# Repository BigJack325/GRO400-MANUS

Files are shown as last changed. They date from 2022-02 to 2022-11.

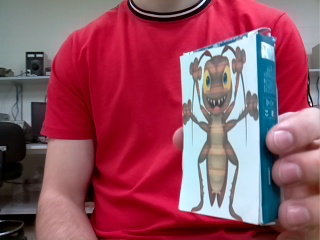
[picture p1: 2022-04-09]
Hexapod-master/Hexapod_Qt/Tensorflow/workspace/images/collectedimages/Angry/Angry.ae11384a-b84e-11ec-aec1-dca632b24006.jpg

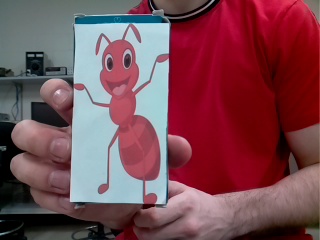
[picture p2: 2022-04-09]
Hexapod-master/Hexapod_Qt/Tensorflow/workspace/images/collectedimages/Happy/Happy.29205612-b84d-11ec-aec1-dca632b24006.jpg

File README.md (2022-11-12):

# GRO400-MANUS
4th Semester Upgraded Hexapod Project for Robotique Engineering Sherbrooke University

<div id="ManUS" align="center">
    <h1>ManUS</h1>
    <h3>Hexapod Robot : Upgraded Version | Promo66-UdeS-GRO</h3>
</div>
<div id="badges" align="center">
    


 

</div>

**This academic project is based on an older academic project from robotic engineering undergraduates at Université de Sherbrooke. "Manu" is an hexapod robot able to interact with his environments. Along with 6 legs comes a camera mounted on a 3D printed head, elevating Manu to a whole new level of robotic hexapod. It can walk, look around and chase targets all around him in a restrained area/arena.**

## Table of Contents
- [Setup](#Setup)
    - [Setup for Users](#SetupUsers)
- [Documentation](#Documentation)
    - [Servos Classification](#Servosclassification)
    - [Assembly Guide](#assemblyguide)
    - [Electrical Schematic](#electricalschematic)
    - [Electrical Diagram of the Shield](#electrical)
    - [Code Overview](#Codeexplication)
- [Robot Operation](#Operation)
    - [Robot Movement](#Movement)
    - [Robot Vision](#Vision)
    - [HMI And Robot Controls](#Controls)
- [External Resources](#Ressources)
    - [Battery, Power Source, and Charger](#Battery)
    - [Microcontroller Board](#Controller)
    - [On-Board Computer](#Computer)
    - [Servomotor for the legs](#Servo1)
    - [Servomotor for the mandibles](#Servo2)
    - [Current Sensor](#Current)
    - [DC/DC Converter](#DCDC)
    - [Fuse 10 Amp](#Fuse)

## Setup

#### Setup for Users

<b>Step 1.</b> Connect Raspberry Pi camera to the Raspberry Pi before booting it up;
<br/>
<b>Step 2.</b> Clone this repository: https://github.com/EDP325/GRO400-MANUS.git
<br/>
<b>Step 3.</b> Create a new virtual environment, install dependencies, and add virtual environment to the Python Kernel by running in terminal:
<pre>
cd ./Hexapod-Master/Hexapod_Qt
./install_venv_pi.sh
</pre> 
<b>Step 4.</b> Connect the hexapod's microcontroller (Arduino) to Raspberry Pi;
<br/>
<b>Step 5.</b> Open the file <b>main.cpp</b> in the <b>./Hexapod-Master/Hexapod_Arduino/src</b> folder, and build the code into the microcontroller with your favorite IDE with PlatformIO;
<br/>
<b>Step 6.</b> Upload the <b>main.cpp</b> in the Arduino;
<br/>
<b>Step 7.</b> Run the file <b>MANUS_QT</b> in the <b>./Hexapod-Master/Hexapod_Qt</b> folder;
<br/>
<b>Step 8.</b> Initialize the serial communication.

## Documentation
#### <a id = "Servosclassification">Classification of the robot servos:</a>

photo patte hexapod

#### <a id= "assemblyguide">Assembly Guide</a>
You need to 3D print the necessary parts that you can find in the *./CAD* folder.   
We have a complete assembly guide [here](https://github.com/EDP325/GRO400-MANUS/wiki):

#### <a id = "electricalschematic"> Electrical Schematic</a>
Schema fritzing
#### <a id= "electrical">Electrical Diagram of the Shield: </a>


#### <a id="Codeexplication">Code Overview</a>

The code is divided in two main sections. The first one is all about the robot's movment and is written in C++ and is run on the Arduino.  This code uses switch cases depending one the manuel/automatic mode and which movment to do.
The second section  includes the vision algorithm and the HMI.  It is written in Python and is run on the Raspberry Pi.  It is made to detect the chosen images and display  the HMI, a screen connected to the Pi.  We chose to use VNCviewer to connect to the Raspberry Pi through Wifi to have a remote connection to the hexapod.

## Robot Operation

#### Robot Movement
The robot can move forward, backward and sideways.  It can also rotate clockwise and counterclockwise.  The head can rotate and the mandibles can open cand close.  

#### Robot Vision
The robot has a vision algorithm that detects these two images: 

happyangry

#### HMI And Robot Controls
Our HMI shows:
- The current view of the cam with TensorFlow AI detection;
- The angles of all the servos;
- A map of the arena with the position of the hexapod;
- Informations for the camera and messages from the Arduino
- Information about battery voltage percentage
- A graphic that shows the the value of a variable over time
- A ComboBox to see every connected ports to initialize serial communication
- Buttons to move the robots



## External ressources

Under this section, you will find external links and descriptions of the project's external resources.

#### Battery

- Brand Name: Makita
- Model:
    - Battery: BL1041B
    - Power Source: PE00000028
    - Charger: DC10SB
- ASIN:
    - Battery: B017GQJDVM
    - Charger: B01FY4XCB0
- Information / Resources:
    - [Makita Battery Webpage](https://www.makitatools.com/products/details/BL1041B)
    - [Makita Power Source Webpage](https://www.makitatools.com/products/details/PE00000028)
    - [Makita Charger Webpage](https://www.makitatools.com/products/details/DC10SB)

#### Microcontroller board

- Brand Name: Arduino
- Model: Mega 2560 R3 (A000067)
- ASIN: B0046AMGW0
- Information / Resources: [Arduino Webpage](https://store.arduino.cc/mega-2560-r3)

#### Onboard computer

- Brand Name: Raspberry Pi
- Model: 3B
- ASIN: B01LPLPBS8
- Information / Resources: [Raspberry Pi Webpage](https://www.raspberrypi.org/products/raspberry-pi-3-model-b/)

#### Servomotor for the legs

- Brand Name : VIPMOON
- Model : MG996R
- Information / Resources : [Amazon Webpage](https://www.amazon.ca/-/fr/gp/product/B07VT5T9JC/ref=ewc_pr_img_1?smid=A2FI4MJY3VQVX5&psc=1)

#### Servomotor for the mandibles

- Model : MG90S
- Information / Resources : [Amazon Webpage](https://www.amazon.ca/servomoteur-h%C3%A9licopt%C3%A8re-m%C3%A9tallique-intelligent-commandes/dp/B08W26FNQD/)
#### Current sensor

- Brand Name : ROBOJAX
- Model : ACS712
- ASIN :B07YP4693C
- Information / Resources : [Amazon Webpage](https://www.amazon.ca/gp/product/B07YP4693C/ref=ppx_yo_dt_b_asin_title_o02_s00?ie=UTF8&psc=1)

#### DC/DC Converter

- Brand Name : Tyenaza
- Model : Tyenazad03xwg94zo
- ASIN :
- Information / Resources : [Amazon Webpage](https://www.amazon.ca/gp/product/B097QT54C7/ref=ppx_yo_dt_b_asin_title_o02_s00?ie=UTF8&amp&psc=1)

#### Pi Camera

- Brand Name : Keyestudio
- Model : 8541582798
- ASIN :
- Information / Resources : [Amazon Webpage](https://www.amazon.ca/gp/product/B073RCXGQS/ref=ppx_yo_dt_b_asin_title_o01_s00?ie=UTF8&psc=1)
    
fuse 10 AMP
#### <a id="Fuse">Fuse 10 AMP 250V</a>

- Brand Name : Littelfuse
- Model : Littelfuse 5x15MM. FAST ACTING 10A.250V.
- Information / Resources :You can buy fuse at any electronics store near your house.  We bought ours [here](https://electro5.com/fr/product/231621/littlefuse-5x15mm-fast-acting-10a250v/)

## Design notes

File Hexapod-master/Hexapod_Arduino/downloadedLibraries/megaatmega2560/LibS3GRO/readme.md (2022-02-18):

# Librairie pour Arduino et carte ArduinoX
voir le wiki pour plus d'informations

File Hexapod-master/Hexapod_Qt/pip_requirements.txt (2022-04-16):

opencv-python-headless
PyQtChart
wget
imutils
ipykernel
lxml

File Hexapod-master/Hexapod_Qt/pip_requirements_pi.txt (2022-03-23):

opencv-python-headless
PyQtChart
imutils
lxml
picamera

https://github.com/google-coral/pycoral/releases/download/v2.0.0/tflite_runtime-2.5.0.post1-cp39-cp39-linux_armv7l.whl

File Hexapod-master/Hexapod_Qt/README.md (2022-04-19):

## Installation on Raspberry-Pi:

<b>Step 1.</b> Activate Raspberry-Pi VNC and  legacy camera using <b>sudo raspy-config</b>  in the interface options selection
<br/>
<b>Step 2.</b> Install VSCode using
<pre>
sudo apt-get code
</pre>
<b>Step 3.</b> Execute the <b>./install_venv_pi.sh</b> in terminal in <b>Hexapod-master/Hexapod_Qt path</b>
<pre>
cd ./Hexapod-Master/Hexapod_Qt
./install_venv_pi.sh
</pre> 
<b>WARNING: PyQt5 installation takes up to 1-2h to compile metadata</b><br>
<br>
<b>Step 4.</b> Enter the virtual environment using
<pre>
source Qt_venv/bin/activate
</pre> 
NOTE: Interpreter in VSCode should automatically change to the virtual environnement

## Installation for TensorFlow(NVIDIA GPU strongly advised):

<b>Step 1.</b> Download [Anaconda](https://www.anaconda.com/products/distribution) and the [Repo](https://github.com/EDP325/GRO400-MANUS.git) on your computer, <b> not Raspberry Pi </b>, then open a terminal. You should see a virtual environnement (base) in the terminal.<br>
<br>
When this environnement is active, you can activate the jupyter notebook using
<pre>
jupiter notebook
</pre>
To deactivate the base environnement, use
<pre>
deactivate
</pre>
<b>Step 2.</b> Execute the <b>./install_venv.sh</b> in terminal in <b>Hexapod-master/Hexapod_Qt path</b>
<pre>
cd ./Hexapod-Master/Hexapod_Qt
./install_venv.sh
</pre>
<b>WARNING: BE SHURE TO ALWAYS BE IN VIRTUAL ENVIRONNEMENT USING</b>
<pre>
source Qt_venv/bin/activate
</pre>
<b>INSIDE THE Hexapod-master/Hexapod_Qt PATH </b>
<br>
<br>
Your terminal should look like this before proceeding<br>


<b>Step 3.</b> Follow this [Github Repo](https://github.com/nicknochnack/TFODCourse) or this [Youtube Video](https://www.youtube.com/watch?v=yqkISICHH-U&t=11796s).<br>
NOTE: Do not use mac computer as they do not have NVIDIA GPU.CPU runtime to teach the TensorFlow can be very long and often do not give good results. When using the 2. Training and Detection, there is code to test if TensorFlow is dectecting NVIDIA GPU. If the code returns False, try updating the GPU to nvidia-470 and look up your GPU driver to see if installed.

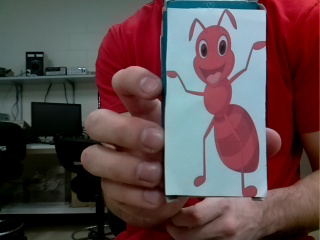
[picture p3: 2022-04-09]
Hexapod-master/Hexapod_Qt/Tensorflow/workspace/images/collectedimages/Happy/Happy.2af7b8cc-b84d-11ec-aec1-dca632b24006.jpg

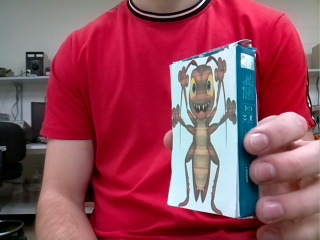
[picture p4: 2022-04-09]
Hexapod-master/Hexapod_Qt/Tensorflow/workspace/images/collectedimages/Angry/Angry.afdc6852-b84e-11ec-aec1-dca632b24006.jpg

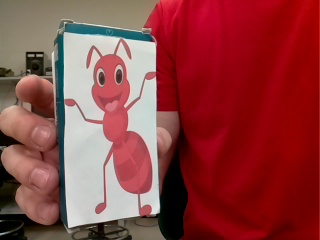
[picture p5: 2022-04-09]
Hexapod-master/Hexapod_Qt/Tensorflow/workspace/images/collectedimages/Happy/Happy.7de9c64c-b84d-11ec-aec1-dca632b24006.jpg

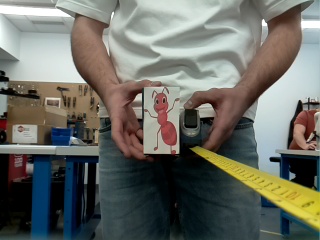
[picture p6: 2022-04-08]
Hexapod-master/Hexapod_Qt/Tensorflow/workspace/images/distance/Distance.jpg

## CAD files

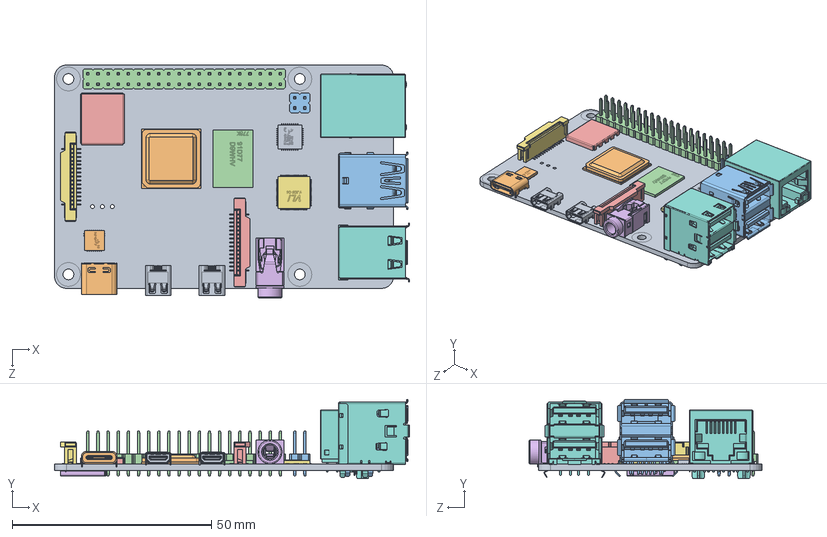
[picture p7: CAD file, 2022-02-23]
CAD/raspberry/Raspberry Pi 4 Model B.SLDASM
89.0 x 19.9 x 58.4 mm
PCB, RPi4ModelB
Broadcom BCM2711B0 CPU, RPi4ModelB
2.54 mm DUPONT MALE PIN HEADER, POE, 2X2, RPi4ModelB
2.54 mm DUPONT MALE PIN HEADER, IO, 2X20, RPi4ModelB
Camera Connector, RPi4ModelB
Microphone Plug, RPi4ModelB
Display Connector, RPi4ModelB
Gigabit Ethernet Port, RPi4ModelB
Female Micro HDMI Connector, RPi4ModelB x 2
Female USB Type C Connector, RPi4ModelB
2X USB3.0 PORTS, RPi4ModelB
91D77 D9WHV 778K, 4 GB LPDDR4 SDRAM, RPi4ModelB
Cypress CYW43455 Wireless Module Cover, RPi4ModelB
SD Card Slot, RPi4ModelB
VIA VL805 PCIe USB 3.0 controller, RPi4ModelB
2X USB2.0 PORTS, RPi4ModelB
Broadcom BCM54213PE Gigabit Ethernet Transceiver, RPi4ModelB
MxL7704 Universal PMIC, RPi4ModelB

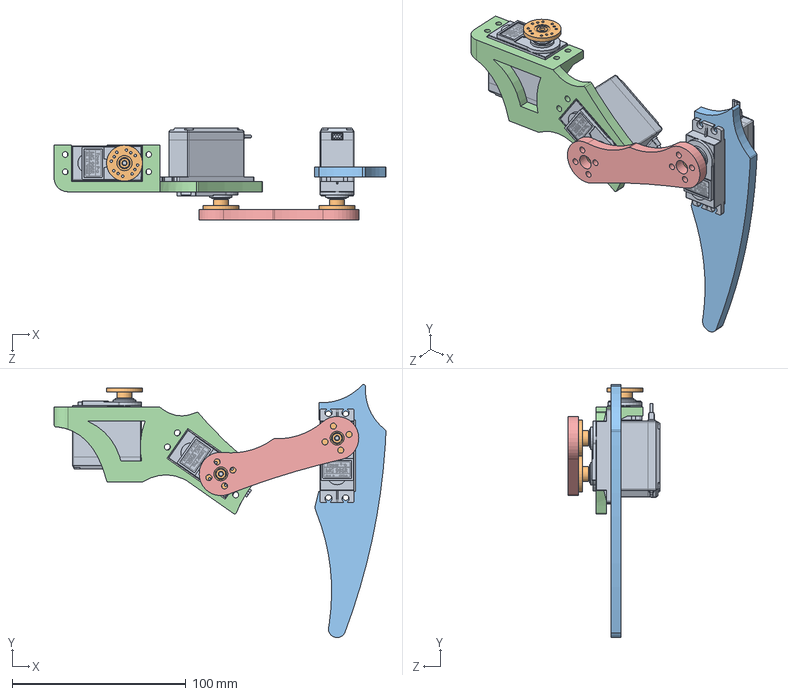
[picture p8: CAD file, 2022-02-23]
CAD/assemblage pate droite.SLDASM
191.2 x 145.7 x 52.9 mm
servoMotorMG996R x 3
attachmentCircular x 3
pate_bas
pate_haut_d
pate_milieu

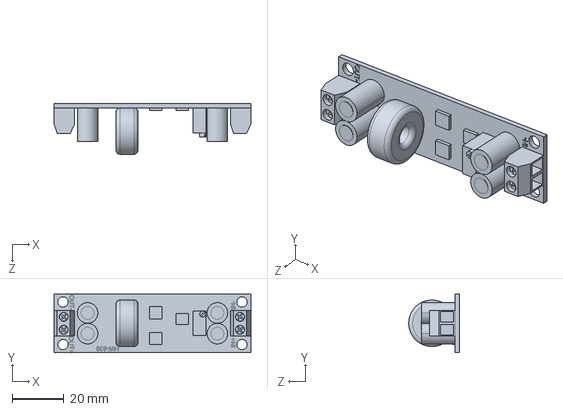
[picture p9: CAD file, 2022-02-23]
CAD/HW636 Power Module v1.SLDASM
76.2 x 22.7 x 19.6 mm

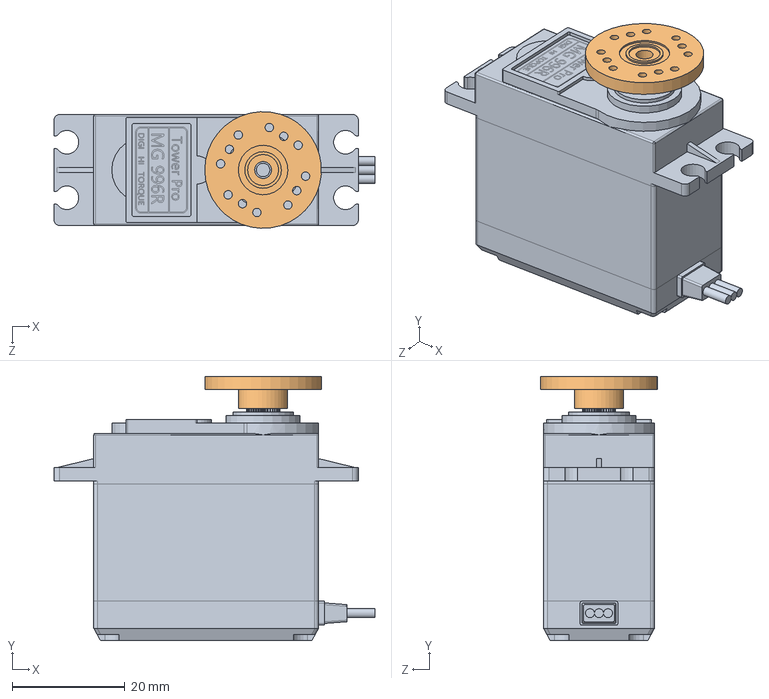
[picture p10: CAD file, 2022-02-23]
CAD/assemblage moteur.SLDASM
57.0 x 46.9 x 20.7 mm
servoMotorMG996R
attachmentCircular

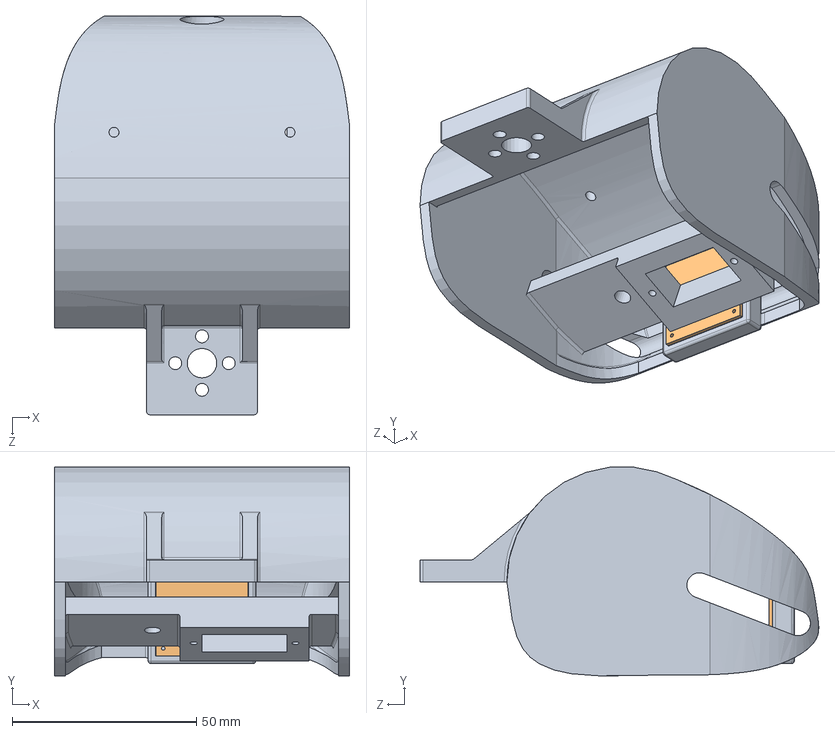
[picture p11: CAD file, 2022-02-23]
CAD/assemblage tete V2.SLDASM
80.0 x 56.6 x 108.1 mm
tete_V2
camera

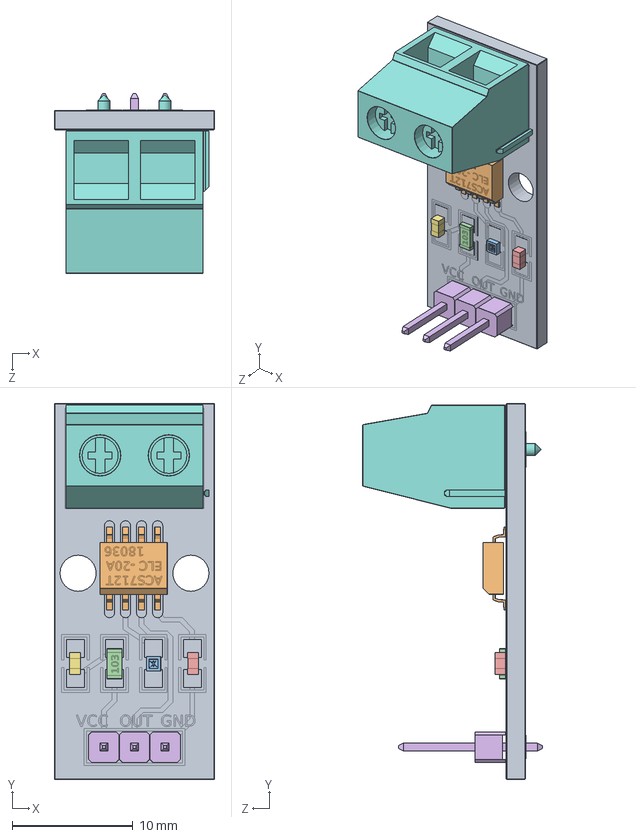
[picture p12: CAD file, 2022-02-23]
CAD/acs712.SLDASM
13.3 x 31.2 x 14.9 mm
ACS712_platine_001.STEP
IC_ACS712_001.STEP
SMD_LED_rot_001.STEP
SMD_R_001.STEP
SMD_DIODE_0.9mm_002.STEP
Pins_3fach_001.STEP
SMD_DIODE_0.9mm_001.STEP
Velleman_145848_001.STEP

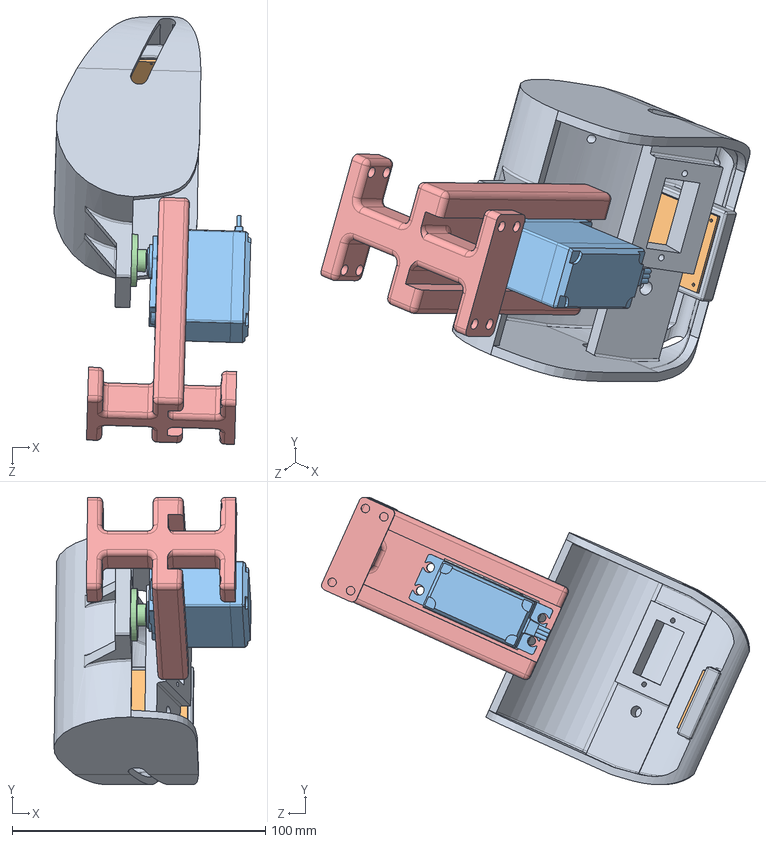
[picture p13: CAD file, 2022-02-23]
CAD/Assemblage tete et cou.SLDASM
77.7 x 113.5 x 169.0 mm
tete_V2
camera
servoMotorMG996R
attachmentCircular
support moteur cou

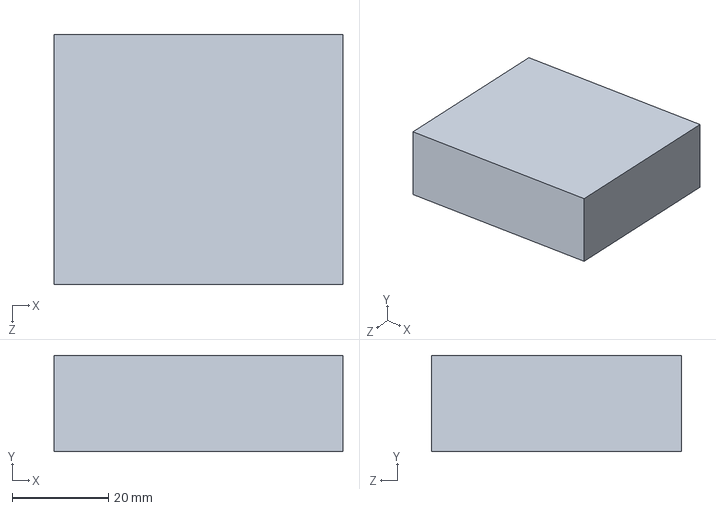
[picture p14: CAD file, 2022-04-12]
CAD/buck converter.SLDPRT
60.0 x 20.0 x 52.0 mm

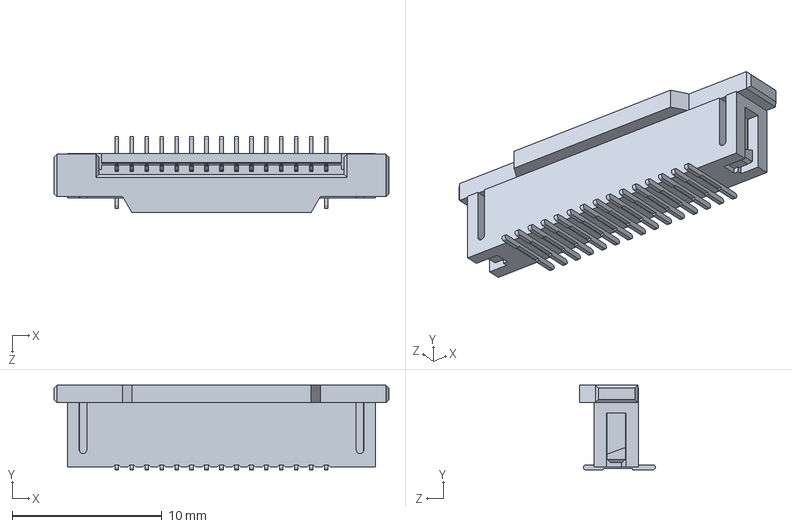
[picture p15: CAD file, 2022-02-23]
CAD/raspberry/Display Connector, RPi4ModelB.SLDPRT
22.4 x 5.68 x 5.07 mm

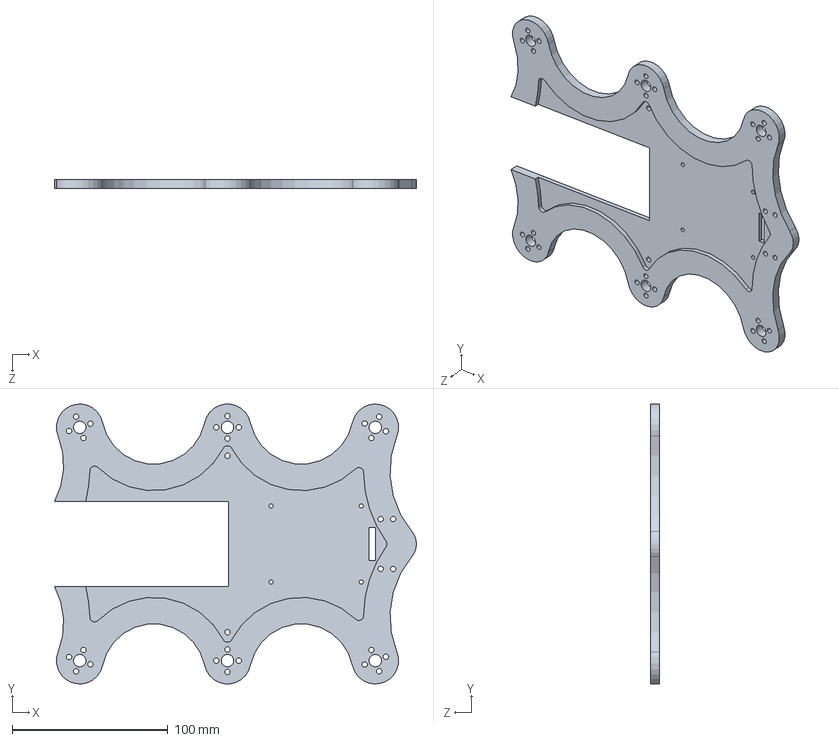
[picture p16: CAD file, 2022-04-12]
CAD/haut corps V2.SLDPRT
232.7 x 179.9 x 6.00 mm

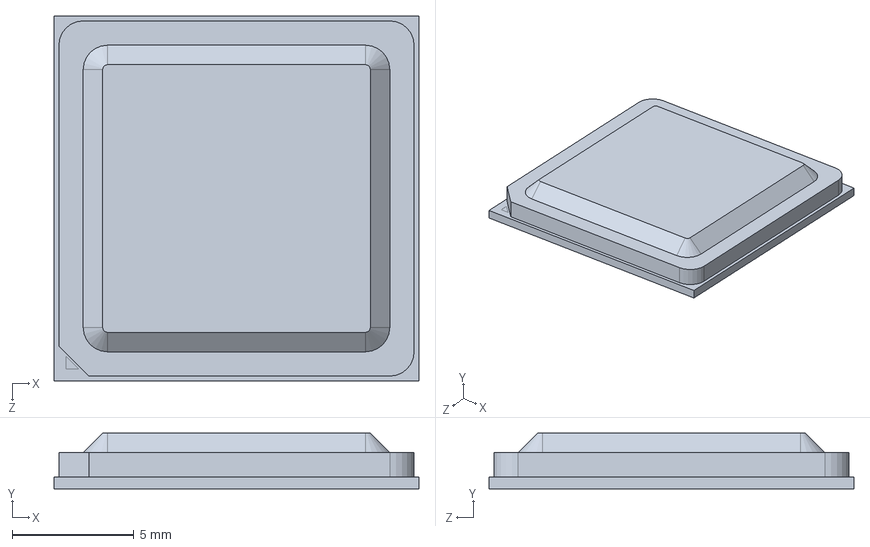
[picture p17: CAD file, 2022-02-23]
CAD/raspberry/Broadcom BCM2711B0 CPU, RPi4ModelB.SLDPRT
15.0 x 2.30 x 15.0 mm

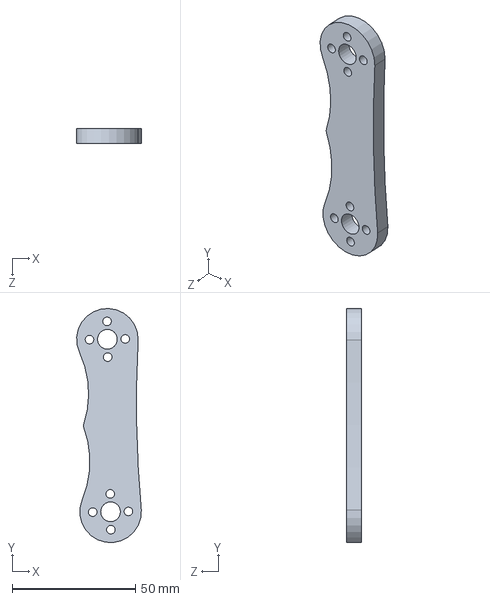
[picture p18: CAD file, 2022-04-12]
CAD/pate_milieu.SLDPRT
26.2 x 94.9 x 6.00 mm

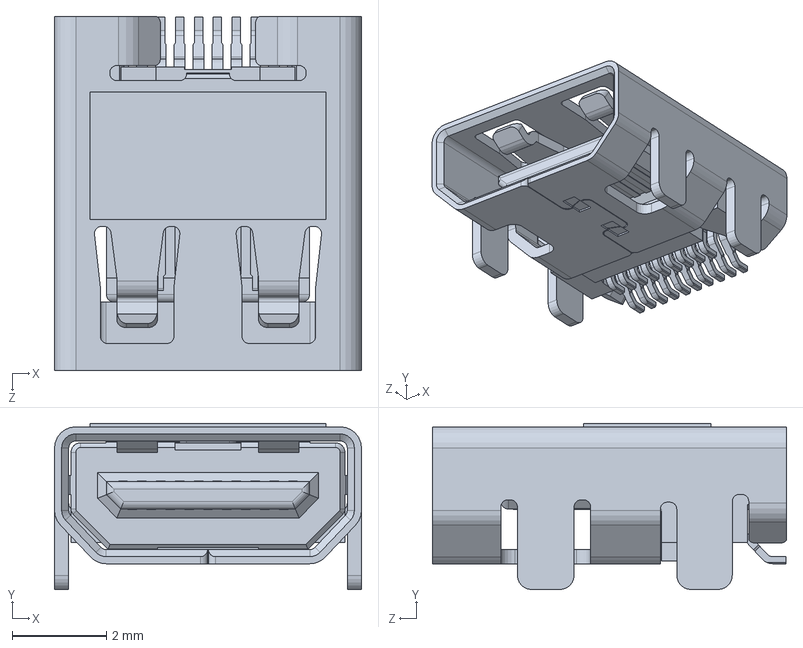
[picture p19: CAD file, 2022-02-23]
CAD/raspberry/Female Micro HDMI Connector, RPi4ModelB.SLDPRT
6.50 x 3.52 x 7.50 mm

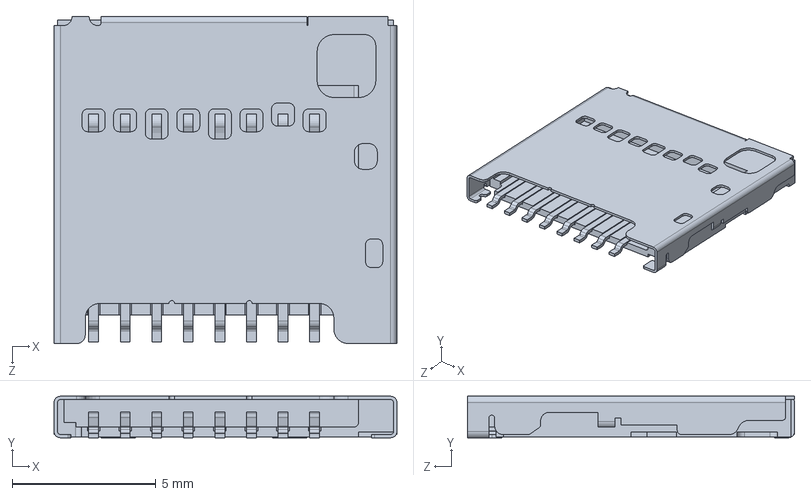
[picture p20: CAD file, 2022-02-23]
CAD/raspberry/SD Card Slot, RPi4ModelB.SLDPRT
11.9 x 1.45 x 11.4 mm

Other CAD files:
CAD/assemblage pate gauche.SLDASM
CAD/support moteur cou.SLDPRT
CAD/Motor_Body2.SLDPRT
CAD/raspberry/Bottom.SLDPRT
CAD/ArduinoMega.SLDPRT
CAD/I beam.SLDPRT
CAD/MAKITA 4.0AH.SLDPRT
CAD/Motor_Body.SLDPRT
CAD/Part1.SLDPRT
CAD/Part2.SLDPRT
CAD/Part3.SLDPRT
CAD/Part4.SLDPRT
CAD/Part5.SLDPRT
CAD/Part6.SLDPRT
CAD/attachmentCircular.SLDPRT
CAD/base corps V2.SLDPRT
CAD/camera.SLDPRT
CAD/cilinder1.SLDPRT
CAD/cilinder2.SLDPRT
CAD/coquille.SLDPRT
CAD/gear1.SLDPRT
CAD/gear2.SLDPRT
CAD/gear3.SLDPRT
CAD/gripper_droite.SLDPRT
CAD/gripper_gauche.SLDPRT
CAD/joint corps.SLDPRT
CAD/joint tete.SLDPRT
CAD/pate_bas.SLDPRT
CAD/pate_haut.SLDPRT
CAD/pate_haut_d.SLDPRT
CAD/proto switch.SLDPRT
CAD/raspberry/2.54 mm DUPONT MALE PIN HEADER, IO, 2X20, RPi4ModelB.SLDPRT
CAD/raspberry/2.54 mm DUPONT MALE PIN HEADER, POE, 2X2, RPi4ModelB.SLDPRT
CAD/raspberry/2X USB2.0 PORTS, RPi4ModelB.SLDPRT
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

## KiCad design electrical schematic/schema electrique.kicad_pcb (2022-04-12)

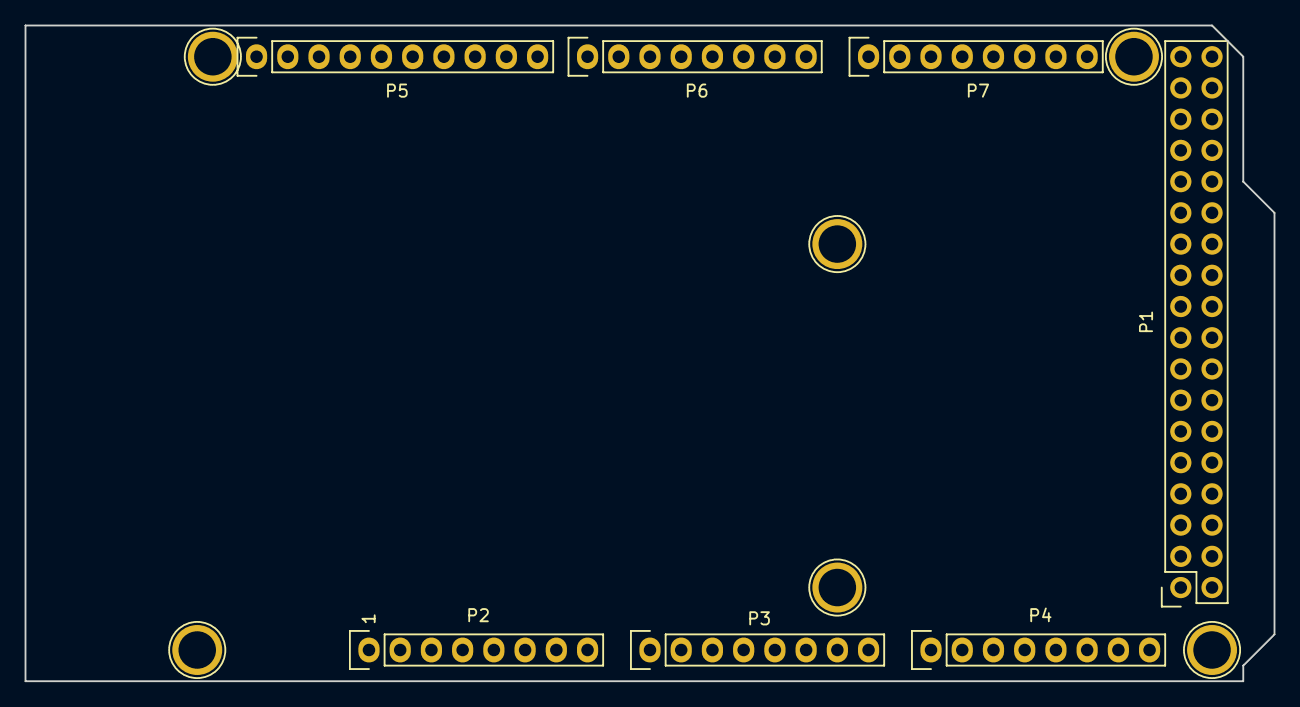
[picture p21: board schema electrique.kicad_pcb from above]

Board: 2 copper layers, 101.6 x 53.3 mm, 13 parts (0 on the bottom side), 2 nets, no tracks yet.

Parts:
P1: Digital; Socket_Strip_Arduino_2x18
P2: Power; Socket_Strip_Arduino_1x08
P3, P4: Analog; Socket_Strip_Arduino_1x08
P5: PWM; Socket_Strip_Arduino_1x10
P6: PWM; Socket_Strip_Arduino_1x08
P7: Communication; Socket_Strip_Arduino_1x08
P8, P9, P10, P11, P12, P13: CONN_01X01; Arduino_1pin

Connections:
+5V: P1.35, P1.36, P2.5
GND: P1.1, P1.2, P2.6, P2.7, P5.4

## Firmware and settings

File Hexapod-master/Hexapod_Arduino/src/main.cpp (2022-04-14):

/* 
 * GRO 400 - Conception d'un robot articulé
 * Auteurs: MANUS
 * date: 25 janvier 2022
*/

/*------------------------------ Librairies ---------------------------------*/
#include <LibS3GRO.h>
#include <ArduinoJson.h>

/*----------------------------- CLASS ----------------------------*/
#define left                           1         // Variable to specify which side the leg is on for inverse cinematic calculation
#define right                          2         // Variable to specify which side the leg is on for inverse cinematic calculation


class SynchServo
{
  public:
     //constructor
    SynchServo();
    SynchServo(MegaServo* servo_1, MegaServo* servo_2,  MegaServo* servo_3, int A_B_or_C, int either_145_or_236, int offset_1, int offset_2, int offset_3);

    int direct_kinematics(int output_dimension, int angleA, int angleB, int angleC);
    int inverse_kinematics(int left_or_right, float X, float Y, float Z);
    void move_angle(int angle_selon__patte_gauche);
    void move_position(float X, float Y, float Z);            // X Y and Z values must be according to left leg
    bool readall(int angle_check);

    MegaServo* servo1;
    MegaServo* servo2;
    MegaServo* servo3;

    int letter;
    int group;

    int offset1;
    int offset2;
    int offset3;

    float L1x;
    float L1y;
    float L1z;
    float L2x;
    float L2y;
    float L2z;
    float L3x;
    float L3y;
    float L3z;

  private:

 
};

//constructor
SynchServo::SynchServo()
{
  letter = 0;
  group  = 0;

  L1x = 1.6;
  L1y = 5.55;
  L1z = 4.72;
  L2x = 0;
  L2y = 7.2;
  L2z = 0;
  L3x = 0;
  L3y = 11.47;
  L3z = -0.5;
}

SynchServo::SynchServo(MegaServo *servo_1, MegaServo *servo_2, MegaServo *servo_3, int  A_B_or_C, int either_145_or_236, int offset_1, int offset_2, int offset_3)
{
  servo1 = servo_1;
  servo2 = servo_2;
  servo3 = servo_3;
  
  letter = A_B_or_C;
  group  = either_145_or_236;

  offset1 = offset_1;
  offset2 = offset_2;
  offset3 = offset_3;

  L1x = 1.6;
  L1y = 5.55;
  L1z = 4.72;
  L2x = 0;
  L2y = 7.2;
  L2z = 0;
  L3x = 0;
  L3y = 11.47;
  L3z = -0.5;
}

int SynchServo::direct_kinematics(int output_dimension, int angleA, int angleB, int angleC)
{
  //cinematic_direct based on left side 
  float theta1 = (angleA)  *2 *PI /360;
  float theta2 = (angleB)  *2 *PI /360;
  float theta3 = (angleC)  *2 *PI /360;

  float length_from_top = L1y + L2y*sin(theta2) + L3y*sin(theta2 + (PI - theta3)); 

  float x_pos = sin(theta1 - PI/2) * length_from_top;
  float y_pos = cos(theta1 - PI/2) * length_from_top;
  float z_pos = 1;

  if(output_dimension == 1)
  {
    return x_pos;
  }
  if (output_dimension == 2)
  {
    return y_pos;
  }
  else
  {
    return z_pos;
  }
  

}

int SynchServo::inverse_kinematics(int left_or_right, float X, float Y, float Z)
{  
  float theta1;
  float theta2;
  float theta3;
  
  // Inverse kinematics relationships
  float r1 = sqrt((X*X) + (Y*Y)) - L1y;
  float r2 = Z;
  float phi2 = atan(r2/r1);
  float r3 = sqrt((r1*r1) + (r2*r2));
  float phi1 = acos( (-(L3y*L3y) + (L2y*L2y) + (r3*r3)) / (2*L2y*r3));
  float phi3 = acos( ((L3y*L3y) + (L2y*L2y) - (r3*r3)) / (2*L2y*L3y));

  
  // Required angles left side
  if(left_or_right == 1)  //if left
  {
    theta1 = atan(Y/-X)     *360/(2*PI);
    if (X == 0) 
    {
      theta1 = 90;
    }
      
    if (X > 0)
    {
      theta1 =  180 - (-theta1);
    }
      
    theta2 =  90 - ((phi2 - phi1)   *360/(2*PI));
    theta3 =  (180 - phi3     *360/(2*PI));
  }

  // Required angles right side
  if(left_or_right == 2)  //if right
  {
    theta1 = atan(Y/-X)     *360/(2*PI);
    if (X == 0) 
    {
      theta1 = 90;
    }
      
    if (X > 0)
    {
      theta1 =  180 - (-theta1);
    }
      
    theta2 =  90 + ((phi2 - phi1)   *360/(2*PI));
    theta3 =  (phi3     *360/(2*PI));
  }

  //return correct angle
  if(letter == 1) //if A
  {
    return theta1;
  }

  if(letter == 2) // if B
  {
    return theta2;
  }

  if(letter == 3) // if C
  {
    return theta3;
  }
  return 0;
}


void SynchServo::move_angle(int angle_selon_patte_gauche)
{
  if (group == 1)
  {
    servo1->write(angle_selon_patte_gauche + offset1);
    servo2->write(180 - (angle_selon_patte_gauche + offset2)); //2400
    servo3->write(angle_selon_patte_gauche + offset3);
  }
  
  if (group == 2)
  {
    servo1->write(180 - (angle_selon_patte_gauche + offset1));
    servo2->write(angle_selon_patte_gauche + offset2);
    servo3->write(180 - (angle_selon_patte_gauche + offset3));
  }
}

void SynchServo::move_position(float X, float Y, float Z)
{
  if(group == 1) //group145
  {
    servo1->write(        inverse_kinematics(left,   X, Y, Z)       );
    servo2->write(        inverse_kinematics(right, -X, Y, Z)       );
    servo3->write(        inverse_kinematics(left,   X, Y, Z)       );

  }

  if(group == 2) //group236
  {
    servo1->write(        inverse_kinematics( right, -X, Y, Z)       );
    servo2->write(        inverse_kinematics( left ,  X, Y, Z)       );
    servo3->write(        inverse_kinematics( right, -X, Y, Z)       );
  }
}

bool SynchServo::readall(int angle_check)
{
  if(group == 1) //group145
  {
    if (servo1->read() == angle_check && servo2->read()== 180 - angle_check && servo3->read() == angle_check)
    {
      return true;
    }
  }

  if(group == 2) //group236
  {
    if (servo1->read() == 180 - angle_check && servo2->read()== angle_check && servo3->read() == 180 - angle_check)
    {
      return true;
    }
  }
  return false;
}


/*------------------------------ Constantes ---------------------------------*/
using namespace std;

#define VIN                            A0
#define BAUD                           115200  // Frequence de transmission serielle
#define UPDATE_PERIODE                 100    // Periode (ms) d'envoie d'etat general

#define MODE_MANUEL                    1         // Used to set robot in manuel mode
#define MODE_AUTOMATIC                 2         // Used to set robot in automatic mode

#define initial_angle_A                90         //Angle of servo A in initialized state
#define initial_angle_B                180         //Angle of servo B in initialized state
#define initial_angle_C                145       //Angle of servo C in initialized state
#define initial_angle_D1               83         //Angle of the neck

#define standing_angle_B               140        // Angle for B servos in standing position
#define standing_angle_C               140        // Angle for C servos in standing position

#define walking_angle_B_increase       20         // Angle to lift up B when walking
#define Walking_angle_A_increase       20         // Angle of servo A used in forward movements

#define sidestep_angle                 10         // Angle used in sidestepping
#define turn_angle                     20         // angle used in turning

#define angle_backward                 20         // Angle of servo A used in backward movements
#define angle_rotation                 20         // Angle of servo A used in spinning movements

#define angle_laydown_B                160          // Angle used to lay robot on ground

#define mandible_open_angle            97         //Servo angle for mandibles to be open
#define mandible_close_angle           130        //Servo angle for mandibles to be closed for grabbing

#define head_turn_angle                15         // Angle the head turns by when calling head to turn

#define arena_sizex                    200                //Width of the arena (cm)
#define arena_sizey                    200                //length of the arena (cm)
#define initial_position_x             arena_sizex/2      //Initial position of the robot on the x axis (cm)
#define initial_position_y             arena_sizey/2      //Initial position of the robot on the y-axis (cm)
#define initial_pos_x_pixel            127                //Initial position x in pixels in hmi
#define initial_pos_y_pixel            123.5              //Initial position y in pixels in hmi

#define map_limit_top_y                43.5               // arena limit position in pixels on hmi
#define map_limit_bottom_y             193.5              // arena limit position in pixels on hmi
#define map_limit_left_x               57.5               // arena limit position in pixels on hmi
#define map_limit_right_x              197                // arena limit position in pixels on hmi


// 43.5 en haut en y ||    193.5 en bas y ||  gauche en x 57.5 || 197 a droite en x || centre 127 en x || centre 123.5 an y

#define turn_error_factor              0.5                  // Error factor when calculating change in orientatio when turning left
#define sidestep_error_factor          0.7

#define offset_front_back              23                 // Angle of offset from middle legs of front and back legs
#define offset_A1                      3  + offset_front_back   //ok
#define offset_A2                      18 + offset_front_back //ok
#define offset_A3                      2    //ok
#define offset_A4                      -9   //ok
#define offset_A5                      2  - offset_front_back //ok
#define offset_A6                      -6 - offset_front_back //ok  
#define offset_B1                      0    //ok
#define offset_B2                      -2   //ok
#define offset_B3                      8    //ok
#define offset_B4                      -2   //ok
#define offset_B5                      4    //ok
#define offset_B6                      2    //ok
#define offset_C1                      4    //ok
#define offset_C2                      7    //
#define offset_C3                      4    //ok
#define offset_C4                      7    //
#define offset_C5                      -1   //ok 
#define offset_C6                      13   //ok
#define offset_D1                      0
#define offset_D2                      0

#define step_delay                     300               // delay between each steps

#define max_current_b4_forced_stop     9.8
#define min_battery_voltage            9.1

#define dropoff_angle_tolerance        15
#define dropoff_x_tolerance            40
#define dropoff_y_tolerance            40

//--- CASE NUMBERS ----
#define INITIALIZATION                 0         // Initial case of the robot when turned on
#define WAIT                           1         // Case when robot is waiting for a command
#define MOVE_FORWARD                   2         // Case for robot to move forward
#define MOVE_BACKWARD                  3         // Case for robot to move backward
#define SIDESTEP_LEFT                  4         // Case for robot to move sideways left
#define SIDESTEP_RIGHT                 5         // Case for robot to move sideways right
#define TURN_LEFT                      6         // Case for robot to spin on itself left
#define TURN_RIGHT                     7         // Case for robot to spin on itself right
#define PICKUP                         8         // Case for robot to pick up object
#define DROP                           9         // Case for robot to drop object
#define STAND                          10        // Case for robot to get up off the ground
#define LAYDOWN                        11        // Case for robot to gently drop to ground
#define HEAD_LEFT                      12        // Case to turn the head to the left
#define HEAD_RIGHT                     13        // Case to turn the head to the right
#define HEAD_CENTRE                    14        // Case to turn head back tostraight position
#define AUTOMATIC                      15        // Case for when the robot is in automatic mode
#define AUTOMATIC_DELAY                16

// --- Class constants
#define A                              1         // Variable to identify which motors is associated with object synchservo
#define B                              2         // Variable to identify which motors is associated with object synchservo
#define C                              3         // Variable to identify which motors is associated with object synchservo
#define group145                       1         // Variable to identify which set of motors is associated with object synchservo
#define group236                       2         // Variable to identify which set of motors is associated with object synchservo
#define left                           1         // Variable to specify which side the leg is on for inverse cinematic calculation
#define right                          2         // Variable to specify which side the leg is on for inverse cinematic calculation

//----------------------------- PINS USED -----------------------------------

                          //Must Change pin numbers
#define A1_Pin                         42  //Digital Port for Servo A1
#define B1_Pin                         41  //Digital Port for Servo B1
#define C1_Pin                         40  //Digital Port for Servo C1

#define A2_Pin                         25  //Digital Port for Servo A2
#define B2_Pin                         26  //Digital Port for Servo B2
#define C2_Pin                         27  //Digital Port for Servo C2

#define A3_Pin                         39  //Digital Port for Servo A3
#define B3_Pin                         38  //Digital Port for Servo B3
#define C3_Pin                         37  //Digital Port for Servo C3
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
void loop() {

  
  if(shouldRead_){
    readMsg();
  }
  if(shouldSend_){
    sendMsg();
  }


  real_current = current();
  real_voltage = battery_voltage();


  if(operation_mode == MODE_MANUEL) // if in manuel mode reset mode automatic
  {
    automatic_done = false;
  } 

  if(which_image != 2)
  {
    object_detected = true;
    image_num = which_image;
  }
  else
  {
    object_detected = false;
  }

  // if(real_current >= max_current_b4_forced_stop)     // If current reaches limit 
  // { 
  //   current_overload = true;
  // }

  if(real_voltage <= min_battery_voltage)             // If voltage reaches lower limit
  { 
    insufficient_voltage = true;
  }

  // if(current_overload == true || insufficient_voltage == true)  // if "voltage or current error" trigger shutdown
  // {
  //   electrical_shutdown = true;
  //   command = WAIT;
  // }
  

  if(robot_is_standing == false && (command != STAND && command != INITIALIZATION))
  {
    command = WAIT;
  }

  if(operation_mode == MODE_AUTOMATIC && !robot_is_standing)
  {
   command = STAND;
  }

//---------------------- SWITCH CASE -------------------------------
 switch(command)
    {
        case INITIALIZATION :      // Sets all servomotors to initial angles

        stepsequence(1, step_delay, &A145_, initial_angle_A);
        stepsequence(2, step_delay, &A236_, initial_angle_A);
        stepsequence(3, step_delay, &B145_, initial_angle_B);
        stepsequence(4, step_delay, &B236_, initial_angle_B);
        stepsequence(5, step_delay, &C145_, initial_angle_C);
        stepsequence(6, step_delay, &C236_, initial_angle_C);
        D1_.write(initial_angle_D1);  
        D2_.write(mandible_open_angle);  

          if (step == 7)
          {
            step = 1;
            command = WAIT;
          }

        break;

        case WAIT :                // Waiting for a command

            t = millis();

            if(operation_mode == MODE_AUTOMATIC && automatic_done == false)
            {
              command = AUTOMATIC_DELAY;
            }
            
            if (electrical_shutdown == true)  //If electrical problem stop moving
            {
            }
            

        break;

        case MOVE_FORWARD :                // Move one step forward sequence
          
          if(future_position(1,1) < arena_sizex && future_position(1,1)> 0)
          {
            if(future_position(1,2) < arena_sizey && future_position(1,2) > 0)
            {
              mouvement_ok = true;
            }
          }

          if(mouvement_ok)
          {
            stepsequence(1, step_delay, &B145_, standing_angle_B + walking_angle_B_increase);
            stepsequence(2, step_delay, &A145_, initial_angle_A + Walking_angle_A_increase);
            stepsequence(3, step_delay, &B145_, standing_angle_B);
            stepsequence(4, step_delay, &B236_, standing_angle_B + walking_angle_B_increase);
            stepsequence(5, step_delay, &A145_, initial_angle_A);
            stepsequence(6, step_delay, &A236_, initial_angle_A + Walking_angle_A_increase);
            stepsequence(7, step_delay, &B236_, standing_angle_B);
            stepsequence(8, step_delay, &B145_, standing_angle_B + walking_angle_B_increase);
            stepsequence(9, step_delay, &A236_, initial_angle_A);
            stepsequence(10, step_delay, &B145_, standing_angle_B);

            if (step == 11)
            {
              step = 1;
              update_position(1);
              mouvement_ok = false;
              command = WAIT;
            }
          }
          else
          {
            command = WAIT;
          }
          

        break;

        case MOVE_BACKWARD :                // Move one step backward sequence
          
          if(future_position(2,1) < arena_sizex && future_position(2,1)> 0)
          {
            if(future_position(2,2) < arena_sizey && future_position(2,2) > 0)
            {
              mouvement_ok = true;
            }
          }

          if(mouvement_ok)
          {

            stepsequence(1, step_delay, &B145_, standing_angle_B + walking_angle_B_increase);
            stepsequence(2, step_delay, &A145_, initial_angle_A - Walking_angle_A_increase);
            stepsequence(3, step_delay, &B145_, standing_angle_B);
            stepsequence(4, step_delay, &B236_, standing_angle_B + walking_angle_B_increase);
            stepsequence(5, step_delay, &A145_, initial_angle_A);
            stepsequence(6, step_delay, &A236_, initial_angle_A - Walking_angle_A_increase);
            stepsequence(7, step_delay, &B236_, standing_angle_B);
            stepsequence(8, step_delay, &B145_, standing_angle_B + walking_angle_B_increase);
            stepsequence(9, step_delay, &A236_, initial_angle_A);
            stepsequence(10,step_delay, &B145_, standing_angle_B);

            if (step == 11)
            {
              step = 1;
              update_position(2);
              mouvement_ok = false;
              command = WAIT;
            }
          }
          else
          {
            command = WAIT;
          }

        break;

        case SIDESTEP_LEFT :                // Lateral step left sequence

          if(future_position(3,1) < arena_sizex && future_position(3,1)> 0)
          {
            if(future_position(3,2) < arena_sizey && future_position(3,2) > 0)
            {
              mouvement_ok = true;
            }
          }

          if (mouvement_ok)
          {
            stepsequence(1, step_delay, &B236_, standing_angle_B + walking_angle_B_increase);
            sidestepsequence(2, step_delay, &C145_, sidestep_angle);
            stepsequence(3, step_delay, &B236_, standing_angle_B);
            stepsequence(4, step_delay, &B145_, standing_angle_B + walking_angle_B_increase);
            sidestepsequence(5, step_delay, &C145_, 0);
            stepsequence(6, step_delay, &B145_, standing_angle_B);

        
            if (step == 7)
            {
              step = 1;
              update_position(3);
              mouvement_ok = false;
              command = WAIT;
            }
          }
          else
          {
            command = WAIT;
          }
        break;

        case SIDESTEP_RIGHT :                // Lateral step right sequence

          if(future_position(4,1) < arena_sizex && future_position(4,1)> 0)
          {
            if(future_position(4,2) < arena_sizey && future_position(4,2) > 0)
            {
              mouvement_ok = true;
            }
          }

          if(mouvement_ok)
          {
            stepsequence(1, step_delay, &B145_, standing_angle_B + walking_angle_B_increase);
            sidestepsequence(2, step_delay, &C236_, sidestep_angle);
            stepsequence(3, step_delay, &B145_, standing_angle_B);
            stepsequence(4, step_delay, &B236_, standing_angle_B + walking_angle_B_increase);
            sidestepsequence(5, step_delay, &C236_, 0);
            stepsequence(6, step_delay, &B236_, standing_angle_B);
        
            if (step == 7)
            {
              step = 1;
              update_position(4);
              mouvement_ok = false;
              command = WAIT;
            }
          }
          else
          {
            command = WAIT;
          }
        break;

        case TURN_LEFT :                // Pivot counter-clockwise sequence
          stepsequence(1, step_delay, &B236_, standing_angle_B + walking_angle_B_increase);
          turnstepsequence(2, step_delay, &A236_, -turn_angle);
          stepsequence(3, step_delay, &B236_, standing_angle_B);
          stepsequence(4, step_delay, &B145_, standing_angle_B + walking_angle_B_increase);
          turnstepsequence(5, step_delay, &A236_, 0);
          stepsequence(6, step_delay, &B145_, standing_angle_B);

           if (step == 7)
          {
            step = 1;
            update_position(5);
            command = WAIT;
          }
        break;

        case TURN_RIGHT :                // Pivot clockwise sequence
          stepsequence(1, step_delay, &B236_, standing_angle_B + walking_angle_B_increase);
          turnstepsequence(2, step_delay, &A236_, turn_angle);
          stepsequence(3, step_delay, &B236_, standing_angle_B);
          stepsequence(4, step_delay, &B145_, standing_angle_B + walking_angle_B_increase);
          turnstepsequence(5, step_delay, &A236_, 0);
          stepsequence(6, step_delay, &B145_, standing_angle_B);

           if (step == 7)
          {
            step = 1;
            update_position(6);
            command = WAIT;
          }
        break;
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

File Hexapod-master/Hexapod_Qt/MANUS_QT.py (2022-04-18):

from cmath import cos, pi, sin
import encodings
from lib2to3.pgen2.pgen import ParserGenerator
import cv2
import re
import time
import numpy as np
import imutils

try:
    from tflite_runtime.interpreter import Interpreter
except:
    pass

from imutils.video import VideoStream
from PyQt5.QtSerialPort import QSerialPort, QSerialPortInfo
from PyQt5.QtWidgets import (QApplication, QGridLayout, QMainWindow, QLabel,
                             QLineEdit, QPushButton, QWidget,
                              QFrame, QComboBox, QGraphicsView, QGraphicsItem, QGraphicsScene,
                               QGraphicsPixmapItem, QPlainTextEdit, QDoubleSpinBox, QTextBrowser, QCheckBox, QSlider)
from PyQt5.QtCore import QRect,QIODevice, QCoreApplication, pyqtSignal, Qt, QTimer, QSize, QThread
from PyQt5.QtGui import QPixmap, QFont, QBrush, QImage, QKeyEvent, QIcon
from PyQt5.QtChart import QChart,QChartView,QLineSeries
import sys, os, json, math

BAUD_RATE = 115200
UI_UPDATE_RATE = 100# Ms
CAM_UPDATE_RATE = 20
NUM_SERVOS = 19
MANUAL_SIDE_MOVEMENT  = 10 #pixels
MANUAL_VERTICAL_MOVEMENT = 10 #pixels
CAMERA_WIDTH = 320
CAMERA_HEIGHT= 320

CUSTOM_MODEL_NAME = 'Ant' 
LABEL_MAP_NAME = 'labelmap.txt'
DISTANCE_IMAGE = 'Distance.jpg'


paths = {
    'DISPLAY_IMAGE_PATH': os.path.join('Qt_Images','Display'),
    'BUTTON_IMAGE_PATH': os.path.join('Qt_Images', 'Buttons'),
    'TFLITE_PATH': os.path.join('Tensorflow', 'workspace','tflite_used_model'),
    'TF_DISTANCE_IMG_PATH': os.path.join('Tensorflow', 'workspace','images','distance',DISTANCE_IMAGE),

 }



class Ui_MainWindow(QMainWindow):

    def __init__(self):
        '''
        This function initializes HMI variables and creates all the objects for the HMI
        '''
        
        super().__init__()

        self.updateTimer = QTimer()
        self.msgBuffer_ = ""
        self.counter = 0
        self.jsondata = None
        self.serialCom_ = None
        self.oldCamMessage = ""

        self.PickDropButtonStatus = "PICK"
        self.StandLayButtonStatus = "STAND"

        self.centralWidget = QWidget(self)
        self.gridLayout = QGridLayout(self.centralWidget)

        # self.widget = QWidget(self.centralWidget)
        self.line = QFrame(self.centralWidget)
        self.Hexapod_Pic = QLabel(self.centralWidget)
        self.Servo = dict()

        for idx in range(1,NUM_SERVOS+1):
            self.Servo[idx] = QLineEdit(self.centralWidget)

        self.RightButton = QPushButton(self.centralWidget)
        self.RightButton.setIcon(QIcon(os.path.join(paths['BUTTON_IMAGE_PATH'],"Right.png")))
        self.RightButton.setIconSize(QSize(61,61))
        self.RightButton.setAutoRepeat(True)
        self.RightButton.setAutoRepeatDelay(UI_UPDATE_RATE+100 )#mseconds
        self.RightButton.setAutoRepeatInterval(UI_UPDATE_RATE+100)#mseconds
        self.RotateRightButton = QPushButton(self.centralWidget)
        self.RotateRightButton.setIcon(QIcon(os.path.join(paths['BUTTON_IMAGE_PATH'],"RotateR.png")))
        self.RotateRightButton.setIconSize(QSize(61,61))
        self.RotateRightButton.setAutoRepeat(True)
        self.RotateRightButton.setAutoRepeatDelay(UI_UPDATE_RATE+100 )#mseconds
        self.RotateRightButton.setAutoRepeatInterval(UI_UPDATE_RATE+100)#mseconds
        self.LeftButton = QPushButton(self.centralWidget)
        self.LeftButton.setIcon(QIcon(os.path.join(paths['BUTTON_IMAGE_PATH'],"Left.png")))
        self.LeftButton.setIconSize(QSize(61,61))
        self.LeftButton.setAutoRepeat(True)
        self.LeftButton.setAutoRepeatDelay(UI_UPDATE_RATE +100)#mseconds        
        self.LeftButton.setAutoRepeatInterval(UI_UPDATE_RATE+100)#mseconds
        self.RotateLeftButton = QPushButton(self.centralWidget)
        self.RotateLeftButton.setIcon(QIcon(os.path.join(paths['BUTTON_IMAGE_PATH'],"RotateL.png")))
        self.RotateLeftButton.setIconSize(QSize(61,61))
        self.RotateLeftButton.setAutoRepeat(True)
        self.RotateLeftButton.setAutoRepeatDelay(UI_UPDATE_RATE+100 )#mseconds
        self.RotateLeftButton.setAutoRepeatInterval(UI_UPDATE_RATE+100)#mseconds
        self.FrontButton = QPushButton(self.centralWidget)
        self.FrontButton.setIcon(QIcon(os.path.join(paths['BUTTON_IMAGE_PATH'],"Front.png")))
        self.FrontButton.setIconSize(QSize(61,61))
        self.FrontButton.setAutoRepeat(True)
        self.FrontButton.setAutoRepeatDelay(UI_UPDATE_RATE+100)#mseconds  
        self.FrontButton.setAutoRepeatInterval(UI_UPDATE_RATE+100)#mseconds
        self.BackButton = QPushButton(self.centralWidget)
        self.BackButton.setIcon(QIcon(os.path.join(paths['BUTTON_IMAGE_PATH'],"Back.png")))
        self.BackButton.setIconSize(QSize(61,61))
        self.BackButton.setAutoRepeat(True)
        self.BackButton.setAutoRepeatDelay(UI_UPDATE_RATE+100 )#mseconds  
        self.BackButton.setAutoRepeatInterval(UI_UPDATE_RATE+100)#mseconds
        self.RotateHeadRightButton = QPushButton(self.centralWidget)
        self.RotateHeadRightButton.setIcon(QIcon(os.path.join(paths['BUTTON_IMAGE_PATH'],"RotateR.png")))
        self.RotateHeadRightButton.setIconSize(QSize(61,61))
        self.RotateHeadRightButton.setAutoRepeat(True)
        self.RotateHeadRightButton.setAutoRepeatDelay(UI_UPDATE_RATE+100 )#mseconds
        self.RotateHeadRightButton.setAutoRepeatInterval(UI_UPDATE_RATE+100)#mseconds
        self.RotateHeadLeftButton = QPushButton(self.centralWidget)
        self.RotateHeadLeftButton.setIcon(QIcon(os.path.join(paths['BUTTON_IMAGE_PATH'],"RotateL.png")))
        self.RotateHeadLeftButton.setIconSize(QSize(61,61))
        self.RotateHeadLeftButton.setAutoRepeat(True)
        self.RotateHeadLeftButton.setAutoRepeatDelay(UI_UPDATE_RATE+100 )#mseconds
        self.RotateHeadLeftButton.setAutoRepeatInterval(UI_UPDATE_RATE+100)#mseconds

        self.PickDropButton = QPushButton(self.centralWidget)

        self.StandLayButton = QPushButton(self.centralWidget)

        self.Port_label = QLabel(self.centralWidget)
        self.comboBoxPort = QComboBox(self.centralWidget)

        self.Map_label = QLabel(self.centralWidget)
        self.MapView = Map(self.centralWidget)

        self.Graph_label = QLabel(self.centralWidget)
        self.graph = QChart()
        self.graphView = QChartView(self.centralWidget)
        self.series_ = QLineSeries()

        self.Donnees_label = QLabel(self.centralWidget)
        self.JsonKey = QLineEdit(self.centralWidget)

        self.Cam_label = QLabel(self.centralWidget)
        self.CamThread = VideoTracking()
        self.CamThread.start()
        self.CamImage = QLabel(self.centralWidget)
        self.CamDistance_label = QLabel(self.centralWidget)
        self.CamDistanceText = QPlainTextEdit(self.centralWidget)

        self.Json_label = QLabel(self.centralWidget)
        self.Json_Browser = QTextBrowser(self.centralWidget)

        self.Manual_mode = QCheckBox(self.centralWidget)
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

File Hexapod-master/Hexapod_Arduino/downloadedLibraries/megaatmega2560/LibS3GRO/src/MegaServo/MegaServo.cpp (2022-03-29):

/*
  MegaServo.cpp - Interrupt driven Servo library for Arduino using 16 bit timers- Version 0.1
  Copyright (c) 2009 Michael Margolis.  All right reserved.

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
  You should have received a copy of the GNU Lesser General Public
  License along with this library; if not, write to the Free Software
  Foundation, Inc., 51 Franklin St, Fifth Floor, Boston, MA  02110-1301  USA
*/

/* 
  This library uses 16 bit timers to drive up to 12 servos on each timer.
  It uses interrupts so no explicit refresh activity is required. 
  The usage and method naming is similar to the Arduino servo library http://www.arduino.cc/en/Reference/Servo
  except that it support up to 48 servos on a Mega (12 on a standard Arduino).
  Also pulse widths can be in microseconds or degrees -
  write() treats parameters less than 200 as degrees, larger values are treated as milliseconds.
 
  
  A servo is activated by creating an instance of the Servo class passing the desired pin to the attach() method.
  The servos are pulsed in the background using the value most recently written using the write() method

  Note that analogWrite of PWM on pins associated with the timer are disabled when the first servo is attached.
  Timers are siezed as needed in groups of 12 servos - 24 servos use two timers, 48 servos will use four.

  The methods are:

   MegaServo - Class for manipulating servo motors connected to Arduino pins.

   attach(pin )  - Attaches a servo motor to an i/o pin.
   attach(pin, min, max  ) - Attaches to a pin setting min and max values in microseconds
    default min is 544, max is 2400  
 
   write()     - Sets the servo angle in degrees.  (invalid angle that is valid as pulse in microseconds is treated as microseconds)
   writeMicroseconds() - Sets the servo pulse width in microseconds 
   read()      - Gets the last written servo pulse width as an angle between 0 and 180. 
   readMicroseconds()   - Gets the last written servo pulse width in microseconds. (was read_us() in first release)
   attached()  - Returns true if there is a servo attached. 
   detach()    - Stops an attached servos from pulsing its i/o pin. 
  
   March 31 2009: initial release 
   Jun 10 2009   : release 2 - added writeMicroseconds method, renamed read_us to readMicroseconds. Added 8MHz clock support
                   fixes to read method and ISR handler when less than maximum number of servo instances
   
 */
#include <avr/interrupt.h>
//#include <WProgram.h> 


#include "MegaServo.h"

#define TICKS_PER_uS     (clockCyclesPerMicrosecond() / 8)  // number of timer ticks per microsecond with prescale of 8

#define SERVOS_PER_TIMER   12                               // the maximum number of servos controlled by one timer 
#define TRIM_DURATION     (SERVOS_PER_TIMER/2)             // compensation ticks to trim adjust for digitalWrite delays 

#define NBR_TIMERS        (MAX_SERVOS / SERVOS_PER_TIMER)
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

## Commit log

2022-02-22 Fixed Serial Port prob
    [MANUS_QT.py, main.cpp]
2022-03-01 Update bouttons et com JSON Pi vers Arduino fonctionne
2022-03-09 Camera HMI
2022-03-09 Code Max main Arduino
2022-03-28 update des librairies megaservo
2022-03-29 Correction des cases
2022-03-30 fonction current sensor
2022-03-30 bon current
2022-03-30 Distance Camera
2022-04-06 pin mode ajouté
2022-04-06 offset servos
2022-04-08 Prevent movement when down
    [main.cpp]
2022-04-08 Button HMI
2022-04-08 correction dune condition if
    [main.cpp]
2022-04-09 Correction de la condition electrical shutdown
    [main.cpp]
2022-04-09 Ajout des case turn head
2022-04-13 correction mapping + backward
    [main.cpp]
2022-04-13 ajout de definition de variable
2022-04-13 correction de limit tourner et garde detection en memoir
    [main.cpp]
2022-04-13 Ajout de mapping pour side step
2022-04-17 plateformio action
2022-04-17 Arduino test

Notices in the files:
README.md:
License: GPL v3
